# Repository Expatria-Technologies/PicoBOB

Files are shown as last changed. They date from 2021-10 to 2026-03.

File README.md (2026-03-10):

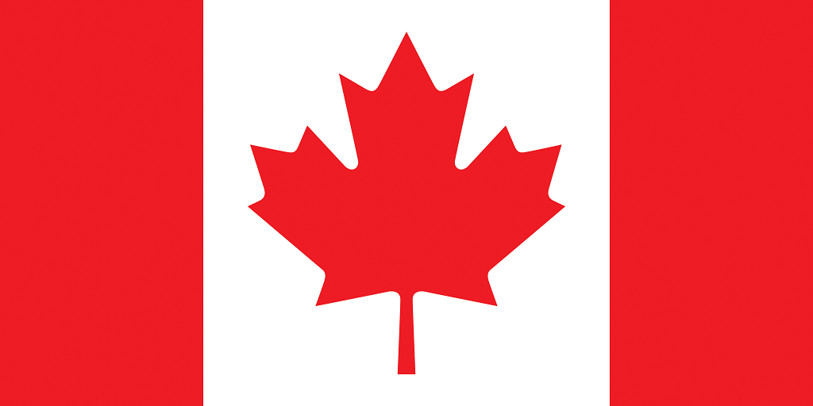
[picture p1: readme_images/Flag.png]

### Canadian-designed open source hardware. For everyone.

# PicoBOB for GRBLHAL

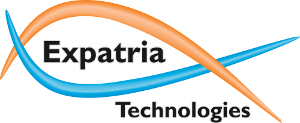
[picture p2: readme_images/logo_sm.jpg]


Expatria Technologies PicoBOB GRBLHAL module

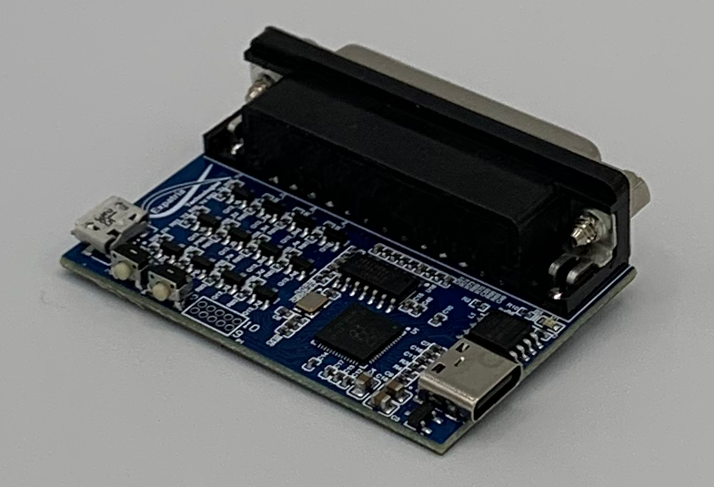
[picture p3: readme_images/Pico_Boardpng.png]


Currently available in our online store:

https://expatria.myshopify.com/products/picobob

Please consider buying a board to support our open-source designs. 

The PicoBOB allows you to use the high performance GRBLHAL motion control system with a traditional Mach3/LinuxCNC parallel-port breakout board.  It is intended to be simple and low cost.  It uses a Raspberry Pi RP2040 MCU and the widely available 5 axis Mach3 breakout board.  It can also be used with the Gecko G540.  The PicoBOB can be easily sourced from JLCPCB.  The complete BOM and fabrications files are in the CAM_OUTPUTS folder for upload.  The design is free to use by all parties, including commercial parties, under the CERN-OHL-S V2 license.  It is our hope that the community finds the design useful and that it may be carried forward to help advance the PrintNC and broader CNC hobby community.

The PicoBOB closely tracks the features of the Mach3 BOB:

1) Up to 5 axes of step/direction control.
3) 10A Spindle relay control.
4) 0-10V analog spindle speed control.
5) 5 general purpose inputs
6) One general purpose output.

The default GRBLHAL builds for the PicoBOB include the following features that are implemented in the RP2040 port of GRBLHAL:

1) Backlash Compensation.
2) Stress-free Autosquaring for the ganged axis
3) Ganged axis offsets to correct for offset homing switches
4) Step rates tested up to 180 KHz on 5 simultaneous axes.

In addition, the board has a USB micro connector for the 5V that is required for the BOB.  There is also a push button to reset the Pi Pico without disconnecting power.

Gerber output files are in the CAM_OUTPUTS folder, along with BOM and Pick and Place files to facilitate easy ordering from JLCPCB.  Now available as a chip-down design in revision B1.  Older A1 revision for Pi Pico module is still hosted in case you want to do the final soldering by hand.  The two designs are functionally identical.

## PicoBOB Overview

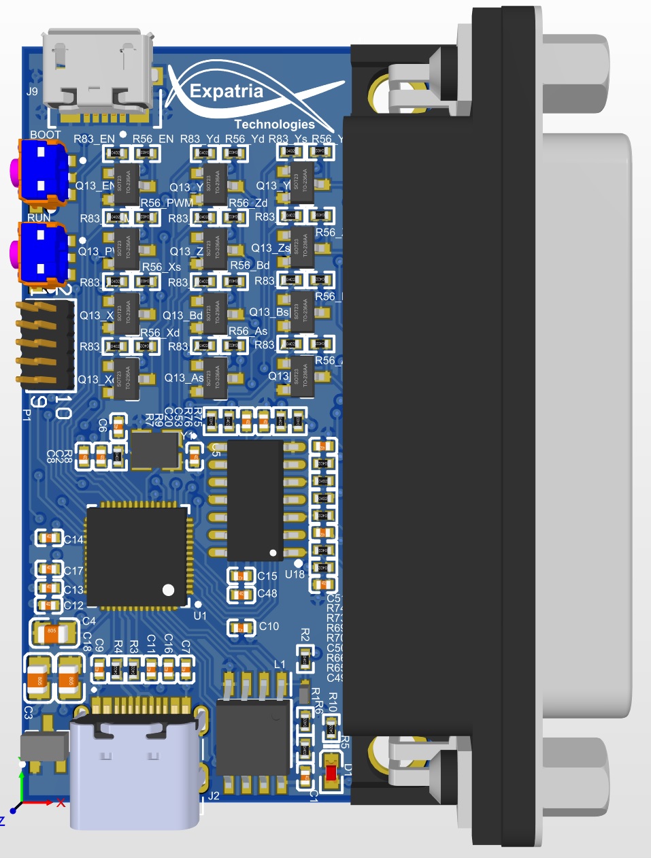
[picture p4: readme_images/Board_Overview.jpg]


Usage notes:

Communication with GRBLHAL on the PicoBOB is accomplished via the USBC connection on the PicoBOB (not connected in above images).  A short USB cable is used to provide the required 5V for the BOB.  In addition, the BOB requires an external 12-24V supply.

The Mach3 BOB shares the B axis direction signal with a spindle relay enable signal - only one can be used at a time.  Also on the PicoBOB, the stepper enable signal is modified in the GRBLHAL default map file so that it is used as the coolant output signal.  All of this is configurable by re-building the GRBLHAL firwmare.

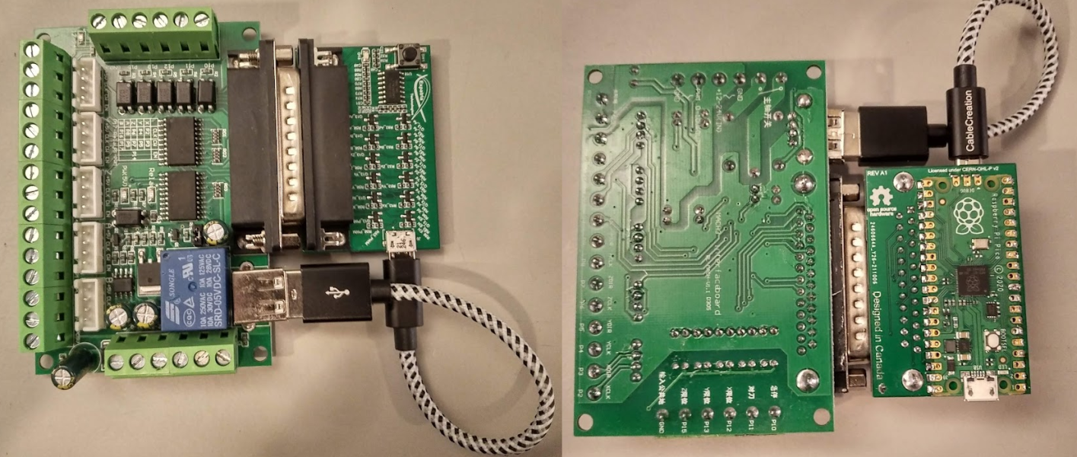
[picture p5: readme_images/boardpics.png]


Above shows the PicoBOB A1 with a Pi Pico installed and connected to the Mach3/LinuxCNC parallel BOB.



Above shows the PicoBOB B1 connected to the Mach3/LinuxCNC parallel BOB.

YGANG pinout is as below:

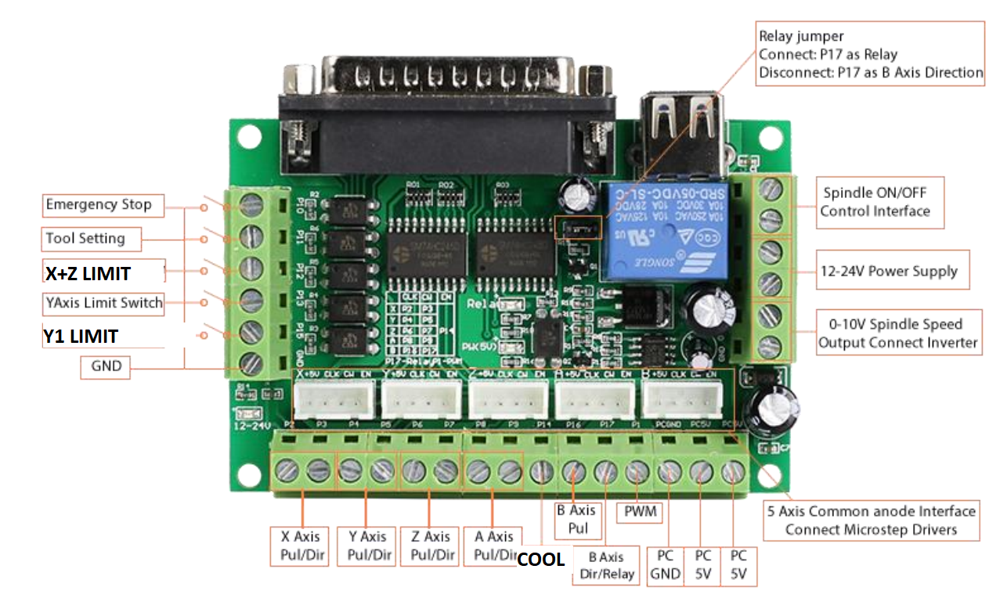
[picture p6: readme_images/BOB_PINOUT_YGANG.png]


To build mainline GRBLHAL firmware, PicoBOB is fully supported by the Web Builder from TerjeIO

http://svn.io-engineering.com:8080/?driver=RP2040&board=PicoBOB

## Gecko Drive G540 support Overview
By using a common "mini gender changer" the PicoBOB can be adapted for use with a G540 4-AXIS Digital Step Drive.

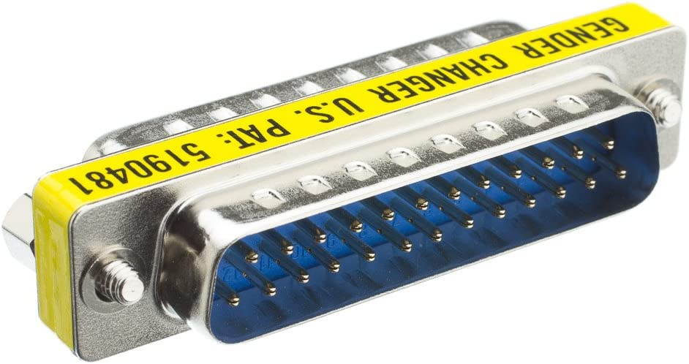
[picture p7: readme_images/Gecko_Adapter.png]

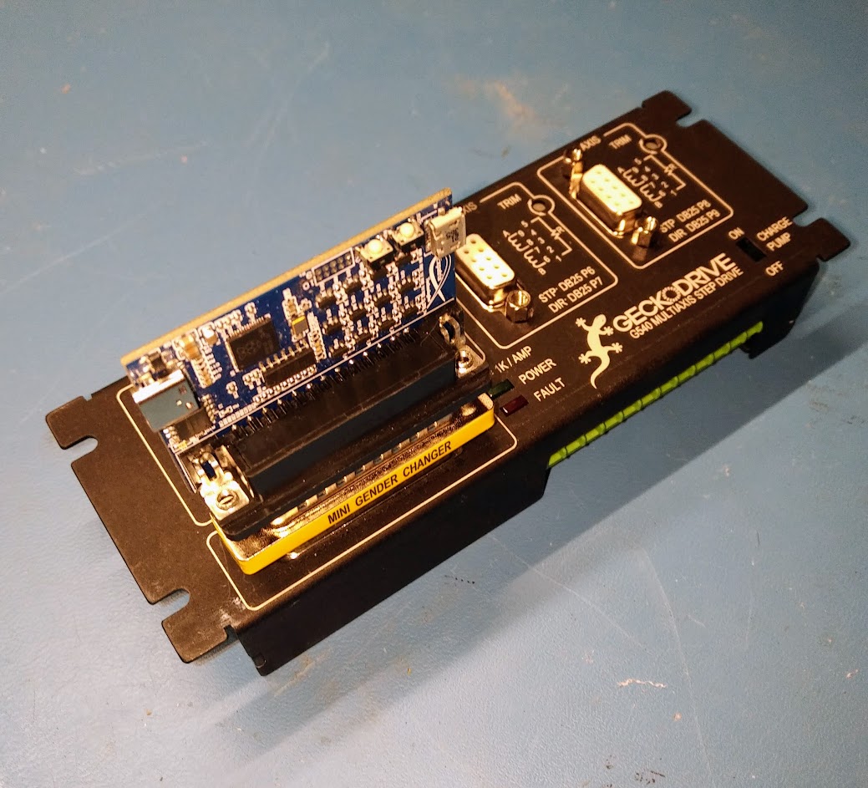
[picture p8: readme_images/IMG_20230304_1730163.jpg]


The updated GRBLHAL map file has the following pinout:

| DB25 Pin | G540 Function | GRBLHAL Function | RP2040 GPIO |
|---|---|---|---|
| Pin 1 | OUTPUT 2 | SPINDLE ENABLE | GPIO14 |
| Pin 2 | X STEP | X STEP | GPIO17 |
| Pin 3 | X DIR | X DIR | GPIO9 |
| Pin 4 | Y SETP | Y SETP | GPIO18 |
| Pin 5 | Y DIR | Y DIR | GPIO10 |
| Pin 6 | Z STEP | Z STEP | GPIO19 |
| Pin 7 | Z DIR | Z DIR | GPIO11 |
| Pin 8 | A STEP | A/M3 STEP | GPIO20 |
| Pin 9 | A DIR | A/M3 DIR | GPIO12 |
| Pin 10 | INPUT 1 | LIMIT XYZ | GPIO3 |
| Pin 11 | INPUT 2 | PROBE | GPIO4 |
| Pin 12 | INPUT 3 | LIMIT A/M3 | GPIO2 |
| Pin 13 | INPUT 4 | HOLD | GPIO1 |
| Pin 14 | VFD PWM | SPINDLE PWM | GPIO16 |
| Pin 15 | FAULT (INPUT 5) | HALT | GPIO5 |
| Pin 16 | CHARGE PUMP | N/A | GPIO21 |
| Pin 17 | OUTPUT 1 | COOLANT | GPIO13 |
| Pin 18-25| GND | | |

For custom builds using the above pinout, you can use this variant from the Web Builder:

http://svn.io-engineering.com:8080/?driver=RP2040&board=PicoBOB_G540

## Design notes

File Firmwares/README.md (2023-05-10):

# Prebuilt PicoBOB Firmwares

Suggestion is to use the aweseom web builder from IO Engineering.

Breakout Board pin mapping:
http://svn.io-engineering.com:8080/?driver=RP2040&board=PicoBOB

Gecko G540 pin mapping:
http://svn.io-engineering.com:8080/?driver=RP2040&board=PicoBOB_G540

Some older testing firmwares are here to help get things up and running.

grblHAL_PicoBOB_3Axis_xxxx.uf2 is for a basic 3 axis machine.

grblHAL_PicoBOB_Ygang__xxxx.uf2 has a ganged Y axis.  This is used on machines like the PrintNC.

grblHAL_PicoBOB_G540YGANG_221229.uf2 has a ganged Y axis and is updated to support the Gecko G540

Install the firmware by putting the Pi Pico into loading mode and copy them to the USB drive that appears.  The PicoBOB is equipped with a reset button for convenience.  With the Pi pico connected to your PC via USB, hold the white button the the Pico and then pulse the black reset button on the other side of the board. The Pico should appear as a USB drive and you can simply copy the desired firmware.

YGANG pinout is as below:



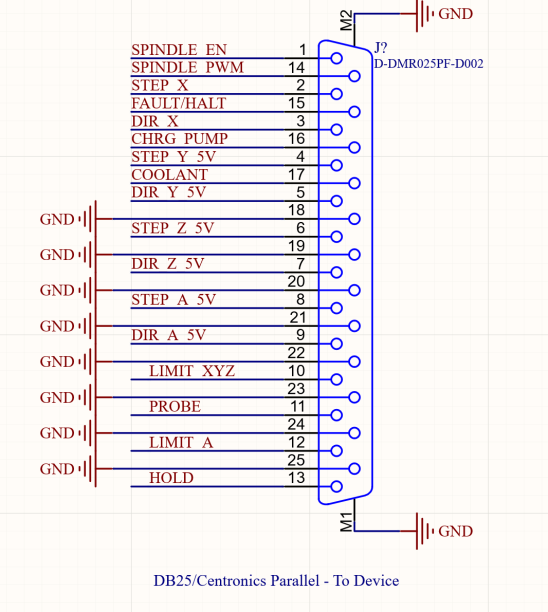
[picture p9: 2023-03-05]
readme_images/g540_pinout.png

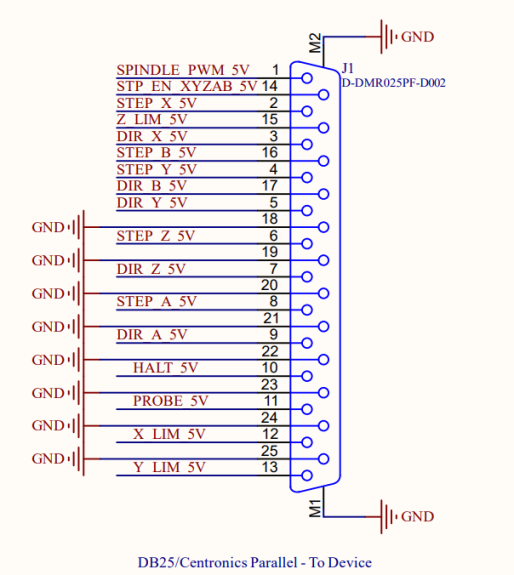
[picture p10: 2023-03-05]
readme_images/picoBOB_Pinout.png

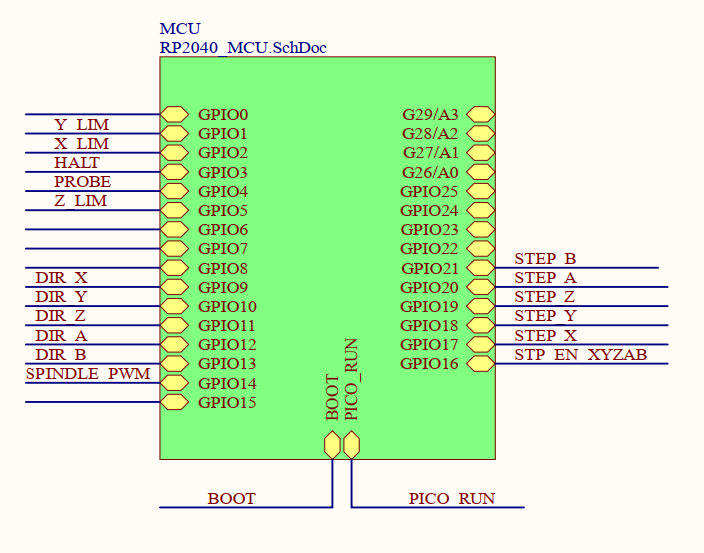
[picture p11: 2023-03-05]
readme_images/default_pinout.png

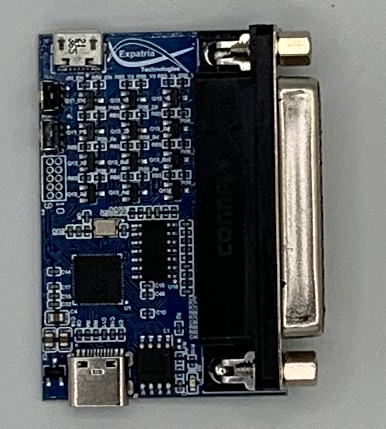
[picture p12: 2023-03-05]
readme_images/Pico_Top.png

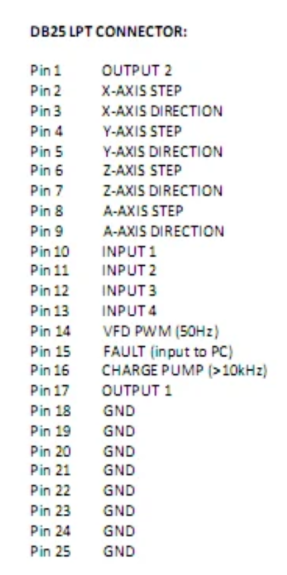
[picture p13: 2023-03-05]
readme_images/G540_DB25_ref.png

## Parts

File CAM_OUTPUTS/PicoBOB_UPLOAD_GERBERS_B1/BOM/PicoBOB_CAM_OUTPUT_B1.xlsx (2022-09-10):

Comment | Description | Designator | Footprint | SuppliersPartNumber | Quantity
100nF | Chip capacitors | C1, C7, C8, C11, C12, C13, C14, C15, C16, C17 | 0402_C | C1525 | 10
4.7uF | Chip capacitor | C2 | 0402_C | C23733 | 1
22uF | Chip capacitors | C3, C4, C18 | 0805_C | C129303 | 3
10pF | Chip capacitors | C5, C6 | 0402_C | C32949 | 2
1.0uF | Chip capacitor | C9, C10, C48 | 0402_C | C52923 | 3
10nF | Chip capacitors | C20, C49, C50, C51, C53 | 0402_C | C15195 | 5
0603 Green | LED | D1 | 0603_LED_S1 | C72043 | 1
D-DMR025PF-D002 | Through Hole,P=2.77mm D-Sub Connectors ROHS | J1 | 618025231121 | C77838 | 1
TYPE-C-31-M-12 | USB Connectors 24 Receptacle 1 8.94*7.3mm RoHS | J2 | HRO_TYPE-C-31-M-12 | C165948 | 1
473460001 | CONN RCPT USB2.0 MICRO B SMD R/A | J9 | FP-473460001-MFG | C132560 | 1
W25Q128JVSIQ_TR | Inductor | L1 | SOIC127P780X195-8N | C97521 | 1
MMBT5551 G1 | 三极管 | Q13_Ad, Q13_As, Q13_Bd, Q13_Bs, Q13_EN, Q13_PWM, Q13_Xd, Q13_Xs, Q13_Yd, Q13_Ys, Q13_Zd, Q13_Zs | SOT-23(SOT-23-3) | C2145 | 12
DNP | Resistor, ±5%, 0.05W | R1 | 0402 |  | 1
1KΩ ±1% | Chip resistor | R2 | 0402_R | C11702 | 1
22Ω ±1% | Chip resistor | R3, R4 | 0402_R | C25092 | 2
5.1KΩ ±1% | Chip resistor | R5, R6, R10 | 0402_R | C25905 | 3
100KΩ ±1% | Chip resistor | R7, R65, R69, R73, R75 | 0402_R | C25741 | 5
470Ω ±1% | Chip resistor | R8 | 0402_R | C25117 | 1
510Ω ±1% | Chip resistor | R9, R56_Ad, R56_As, R56_Bd, R56_Bs, R56_EN, R56_PWM, R56_Xd, R56_Xs, R56_Yd, R56_Ys, R56_Zd, R56_Zs, R66, R70, R74, R76 | 0402_R | C25123 | 17
2.2KΩ ±1% | Chip resistor | R83_Ad, R83_As, R83_Bd, R83_Bs, R83_EN, R83_PWM, R83_Xd, R83_Xs, R83_Yd, R83_Ys, R83_Zd, R83_Zs | 0402_R | C25879 | 12
SKRTLAE010 | Side Push Type, 250 V, -40 to 90 degC, 3-Pin SMD, RoHS, Tape and Reel | SW1, SW2 | ALPS-SKRTLAE010_V | C110293 | 2
RP2040 | RP2040 First MCU from RPI | U1 | RP2040 |  | 1
74HC14D | 74系列逻辑芯片 | U18 | SOIC-14_150mil | C5605 | 1
XC6206P332MR | 200mA 680mV@(100mA) Fixed 3.3V~3.3V Positive 1 6V SOT-23-3L Linear Voltage Regulators (LDO) ROHS | VR1 | SOT-23-3L | C5446 | 1
YSX321SL | Crystal or Oscillator | Y1 | YSX321SL | C9002 | 1

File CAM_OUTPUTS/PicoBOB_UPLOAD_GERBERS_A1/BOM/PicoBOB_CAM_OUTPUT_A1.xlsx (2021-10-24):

Comment | Description | Designator | Footprint | SuppliersPartNumber | Quantity
10nF | Chip capacitors | C20, C49, C50, C51, C53 | 0402_C | C15195 | 5
100nF | Chip capacitors | C23 | 0402_C | C1525 | 1
1.0uF | Chip capacitor | C48 | 0402_C | C52923 | 1
0805 Green | LED | D15 | 0805_LED_S1 | C2297 | 1
D-DMR025PF-D002 | Through Hole,P=2.77mm D-Sub Connectors ROHS | J1 | 618025231121 | C190083 | 1
PICO | Connector | J8 | PICO |  | 1
473460001 | CONN RCPT USB2.0 MICRO B SMD R/A | J9 | FP-473460001-MFG | C132560 | 1
MMBT5551 G1 | 三极管 | Q13_Ad, Q13_As, Q13_Bd, Q13_Bs, Q13_EN, Q13_PWM, Q13_Xd, Q13_Xs, Q13_Yd, Q13_Ys, Q13_Zd, Q13_Zs | SOT-23(SOT-23-3) | C2145 | 12
100KΩ ±1% | Chip resistor | R7, R65, R69, R73, R75 | 0402_R | C25741 | 5
510Ω ±1% | Chip resistor | R9, R56_Ad, R56_As, R56_Bd, R56_Bs, R56_EN, R56_PWM, R56_Xd, R56_Xs, R56_Yd, R56_Ys, R56_Zd, R56_Zs, R66, R70, R74, R76 | 0402_R | C25123 | 17
10KΩ ±1% | Chip resistor | R52 | 0402_R | C25744 | 1
1.2KΩ ±1% | Chip resistor | R59 | 0402_R | C25862 | 1
2.2KΩ ±1% | Chip resistor | R83_Ad, R83_As, R83_Bd, R83_Bs, R83_EN, R83_PWM, R83_Xd, R83_Xs, R83_Yd, R83_Ys, R83_Zd, R83_Zs | 0402_R | C25879 | 12
K2-1102SP-C4SC-04 | Top Actuated 50mA @ 12VDC Round Button SPST 6*6mm Tactile Switches ROHS | SW1 | TECO-FSM4JSMATR_V | C127509 | 1
74HC14D | 74系列逻辑芯片 | U18 | SOIC-14_150mil | C5605 | 1

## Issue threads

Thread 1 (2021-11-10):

Question: JLCPCB

oke24, 2021-11-10:
Hi , a short question - for SMT Assembly at JLCPCB I need a CPL file.
I couldn't find this file in the PicoBOB directory structure. It it possible to generate this file and copy into the CAM_OUTPUTS folder ? Thanky you very much !

andrewmarles, 2021-11-11:
You should use the csv in the pick and place folder.

oke24, 2021-11-11:
Thanks!

Closed 2021-11-11.

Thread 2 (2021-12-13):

Can this be bought?

Cncninja, 2021-12-13:
anywhere to buy this ?

andrewmarles, 2021-12-13:
Best way to get one is to use the provided files and just order a couple assembled from JLCPCB.

Closed 2021-12-20.

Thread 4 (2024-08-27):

Maximum step rate

jamesbaber, 2024-08-27:
Hello,

I've purchased a PicoBOB and was hoping to utilise the claimed maximum step rate of 180k steps/sec.
My oscilloscope shows a stable pulse up until around 60 kHz with very narrow gaps between pulses. If I try to continue up to 70 kHz, the pulse gaps disappear and it becomes one solid pulse with a few glitches.

At 60kHz, the gaps are ~490 ns long and exhibit very square edges once passed through the SN74HC245 bus transceivers on the Mach3 BOB. Before the buffer, they have rounder edges and still do not properly form at higher frequencies.
I am trying to jog the board from ioSender 2.0.44.

I've tried the PicoBOB and PicoBOB_G540 boards on the grblHAL Web Builder with the same results.
Can you please let me know what the test conditions were for the 180kHz pulse rate spec?

Thanks!

andrewmarles, 2024-08-27:
You can try reducing the pulse width in your stepper settings.

jamesbaber, 2024-08-27:
@andrewmarles

Thank you, I did not expect such granular controls to exist!
This has resolved my issue.

Closed 2024-08-27.

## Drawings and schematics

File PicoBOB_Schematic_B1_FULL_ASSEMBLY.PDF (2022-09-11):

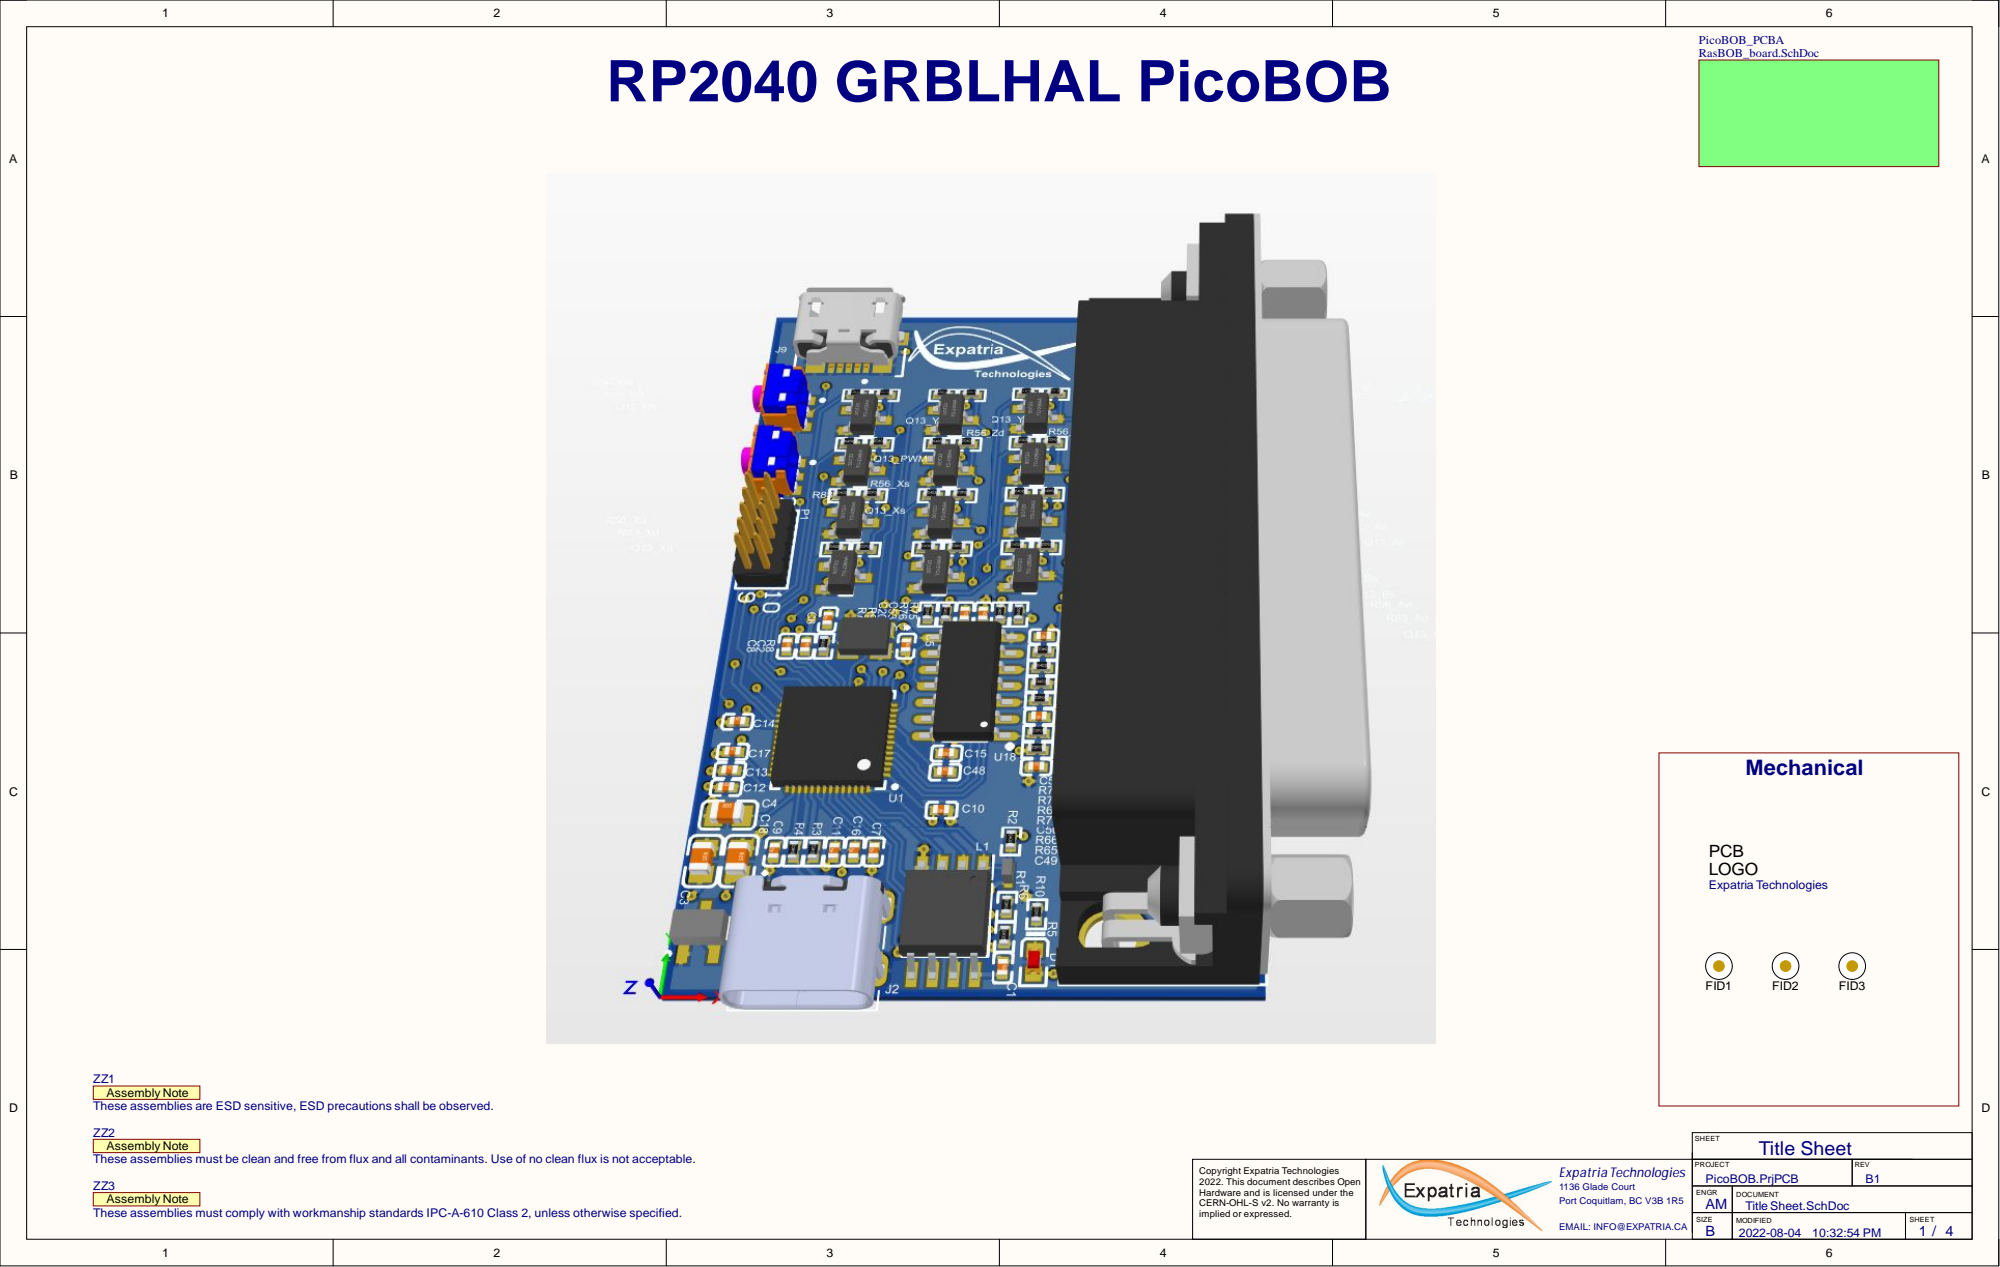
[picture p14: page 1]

Assembly Note
These assemblies are ESD sensitive, ESD precautions shall be observed.

These assemblies must be clean and free from flux and all contaminants. Use of no clean flux is not acceptable.

Copyright Expatria Technologies 2022. This document describes Open Hardware and is licensed under the CERN-OHL-S v2. No warranty is implied or expressed. | | PROJECT PicoBOB.PrjPCB | REV B1

These assemblies must comply with workmanship standards IPC-A-610 Class 2, unless otherwise specified.

ENGR AM | DOCUMENT Title Sheet.SchDoc

SIZE B | MODIFIED 2022-08-04 10:32:54 PM | SHEET 1 / 4

EMAIL: INFO@EXPATRIA.CA

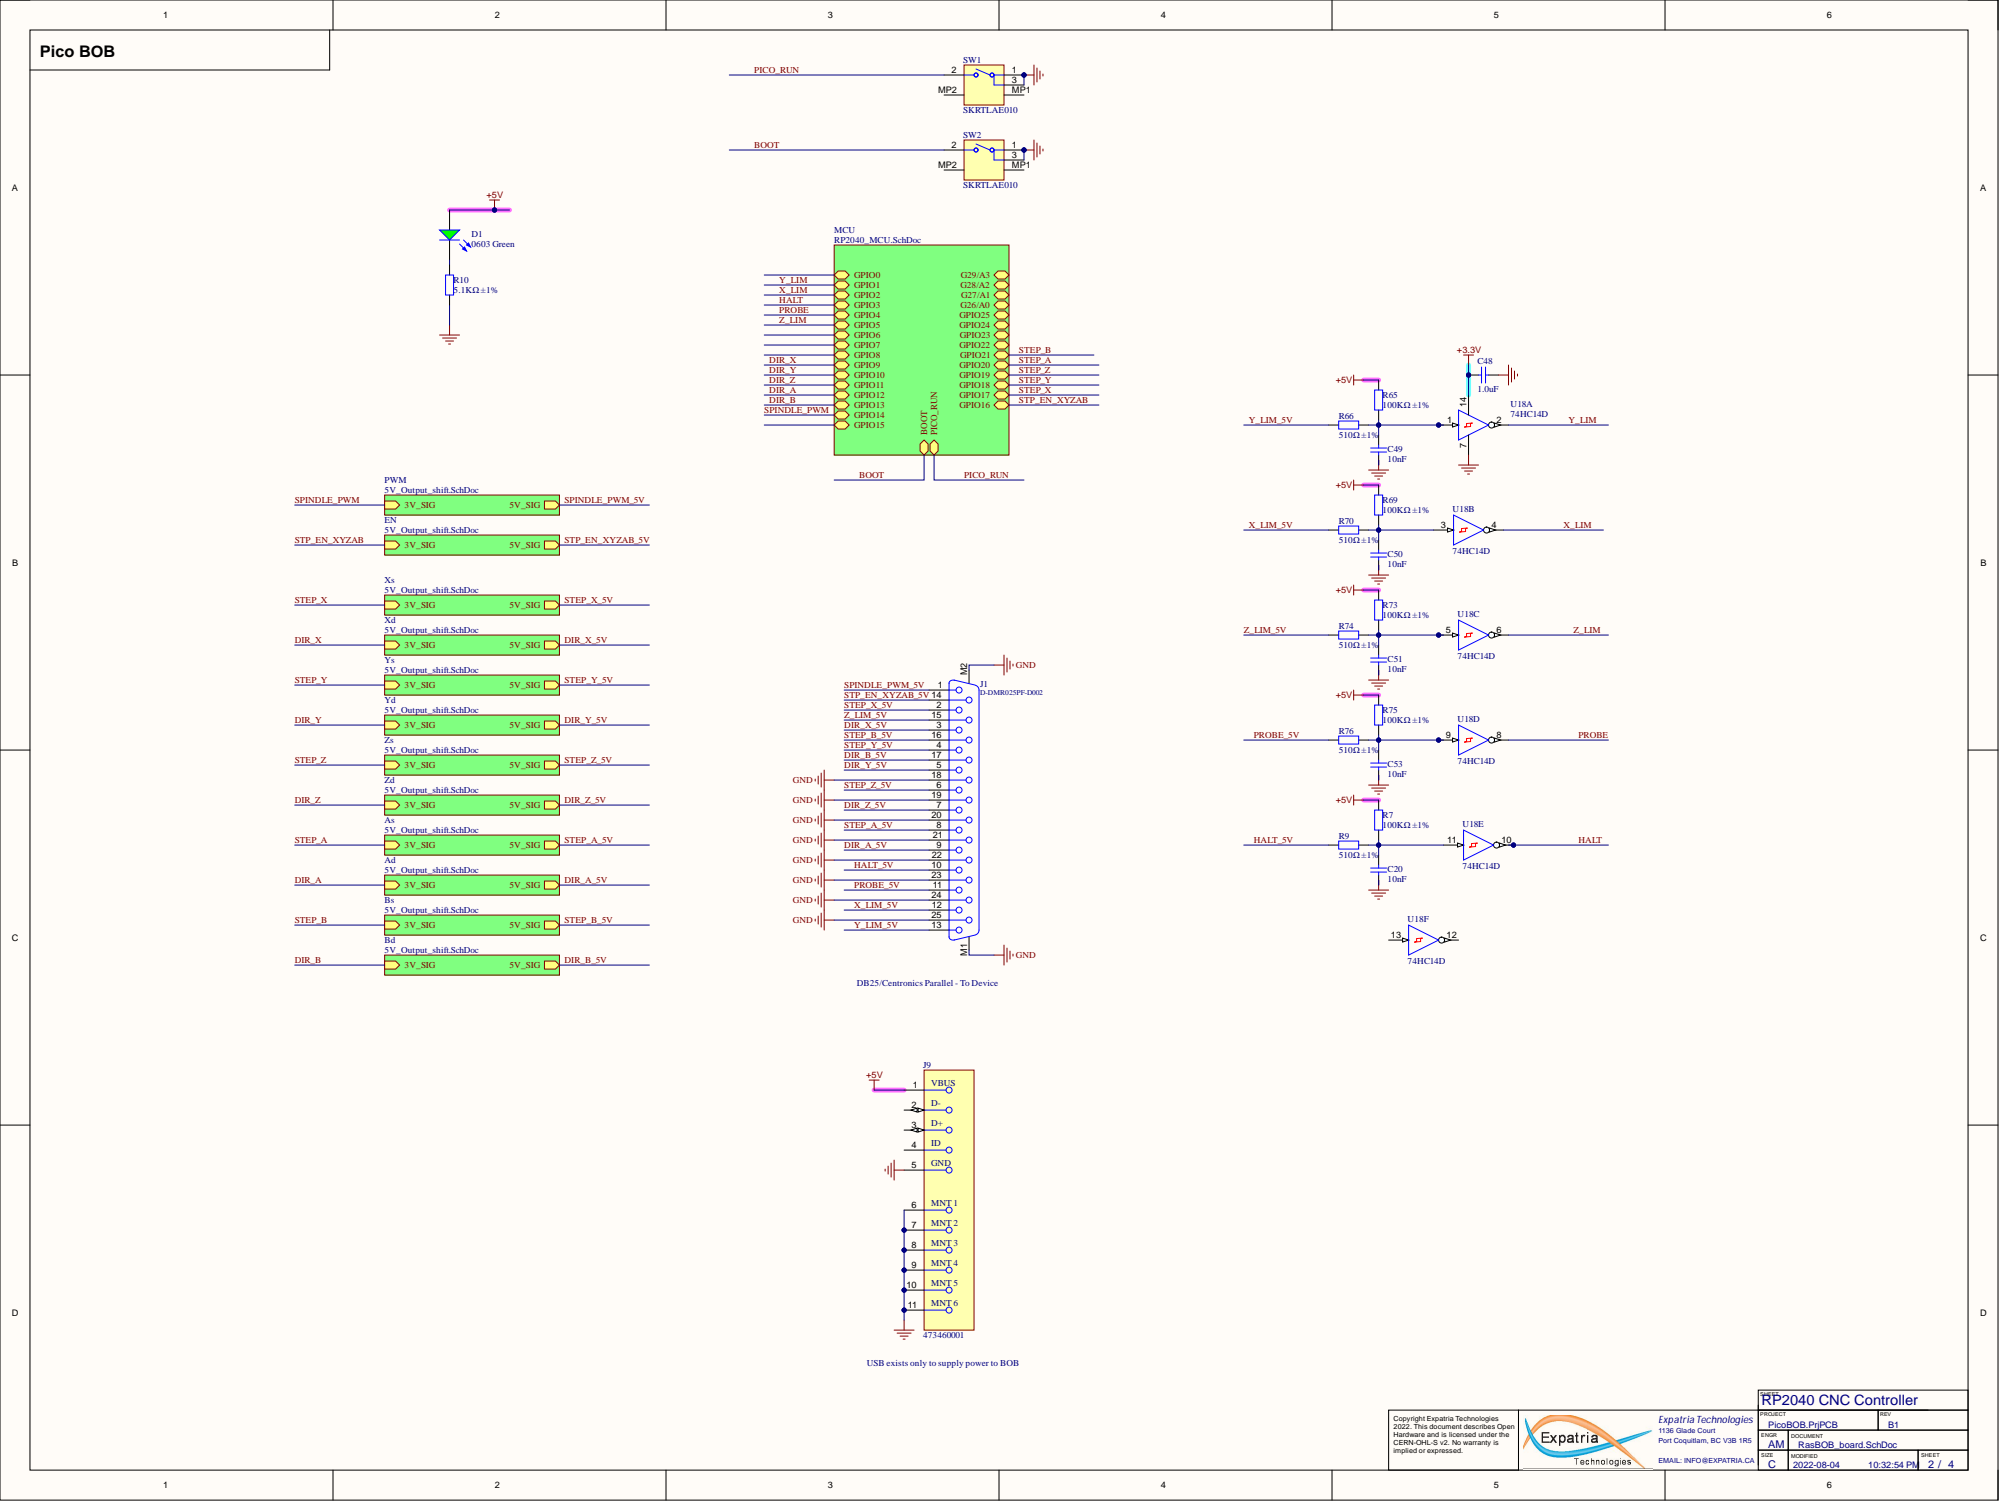
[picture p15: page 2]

Hardware a n d i s l i e s d u er th CERN-OHL-S v 2. No warra nty i m p or x pre . | | P OJE PicoBOB.Prj | R V

B Copyright Expatria Technologies 2022. This document describes Open

N G A | U RasBOB_board.Sc h D o c

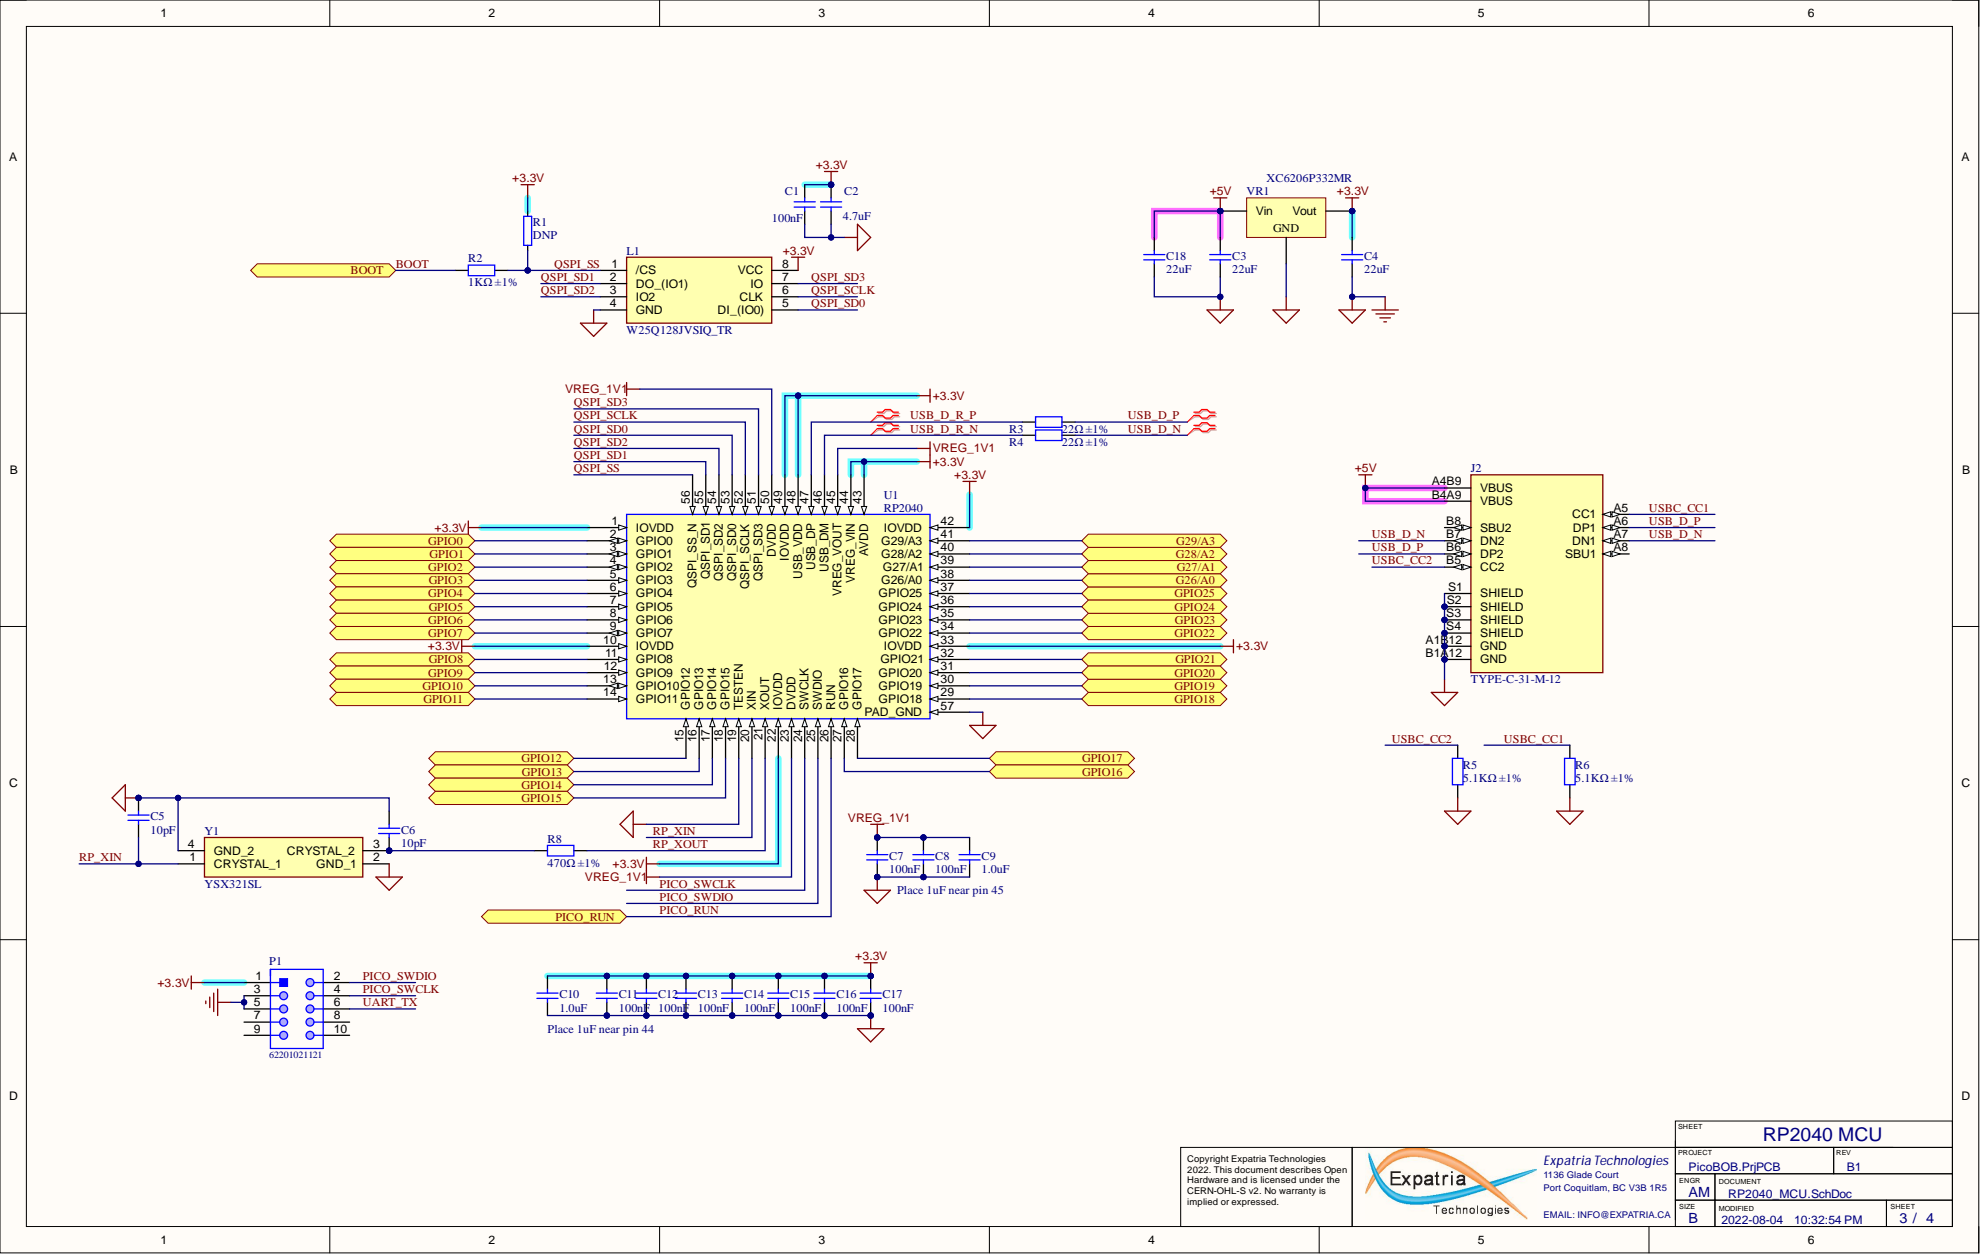
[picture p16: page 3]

QSPI_SD2
QSPI_SD1
QSPI_SS

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

ENGR AM | DOCUMENT RP2040_MCU.SchDoc

SIZE | MODIFIED 2022-08-04 10:32:54 PM | SHEET 3 / 4

EMAIL: INFO@EXPATRIA.CA

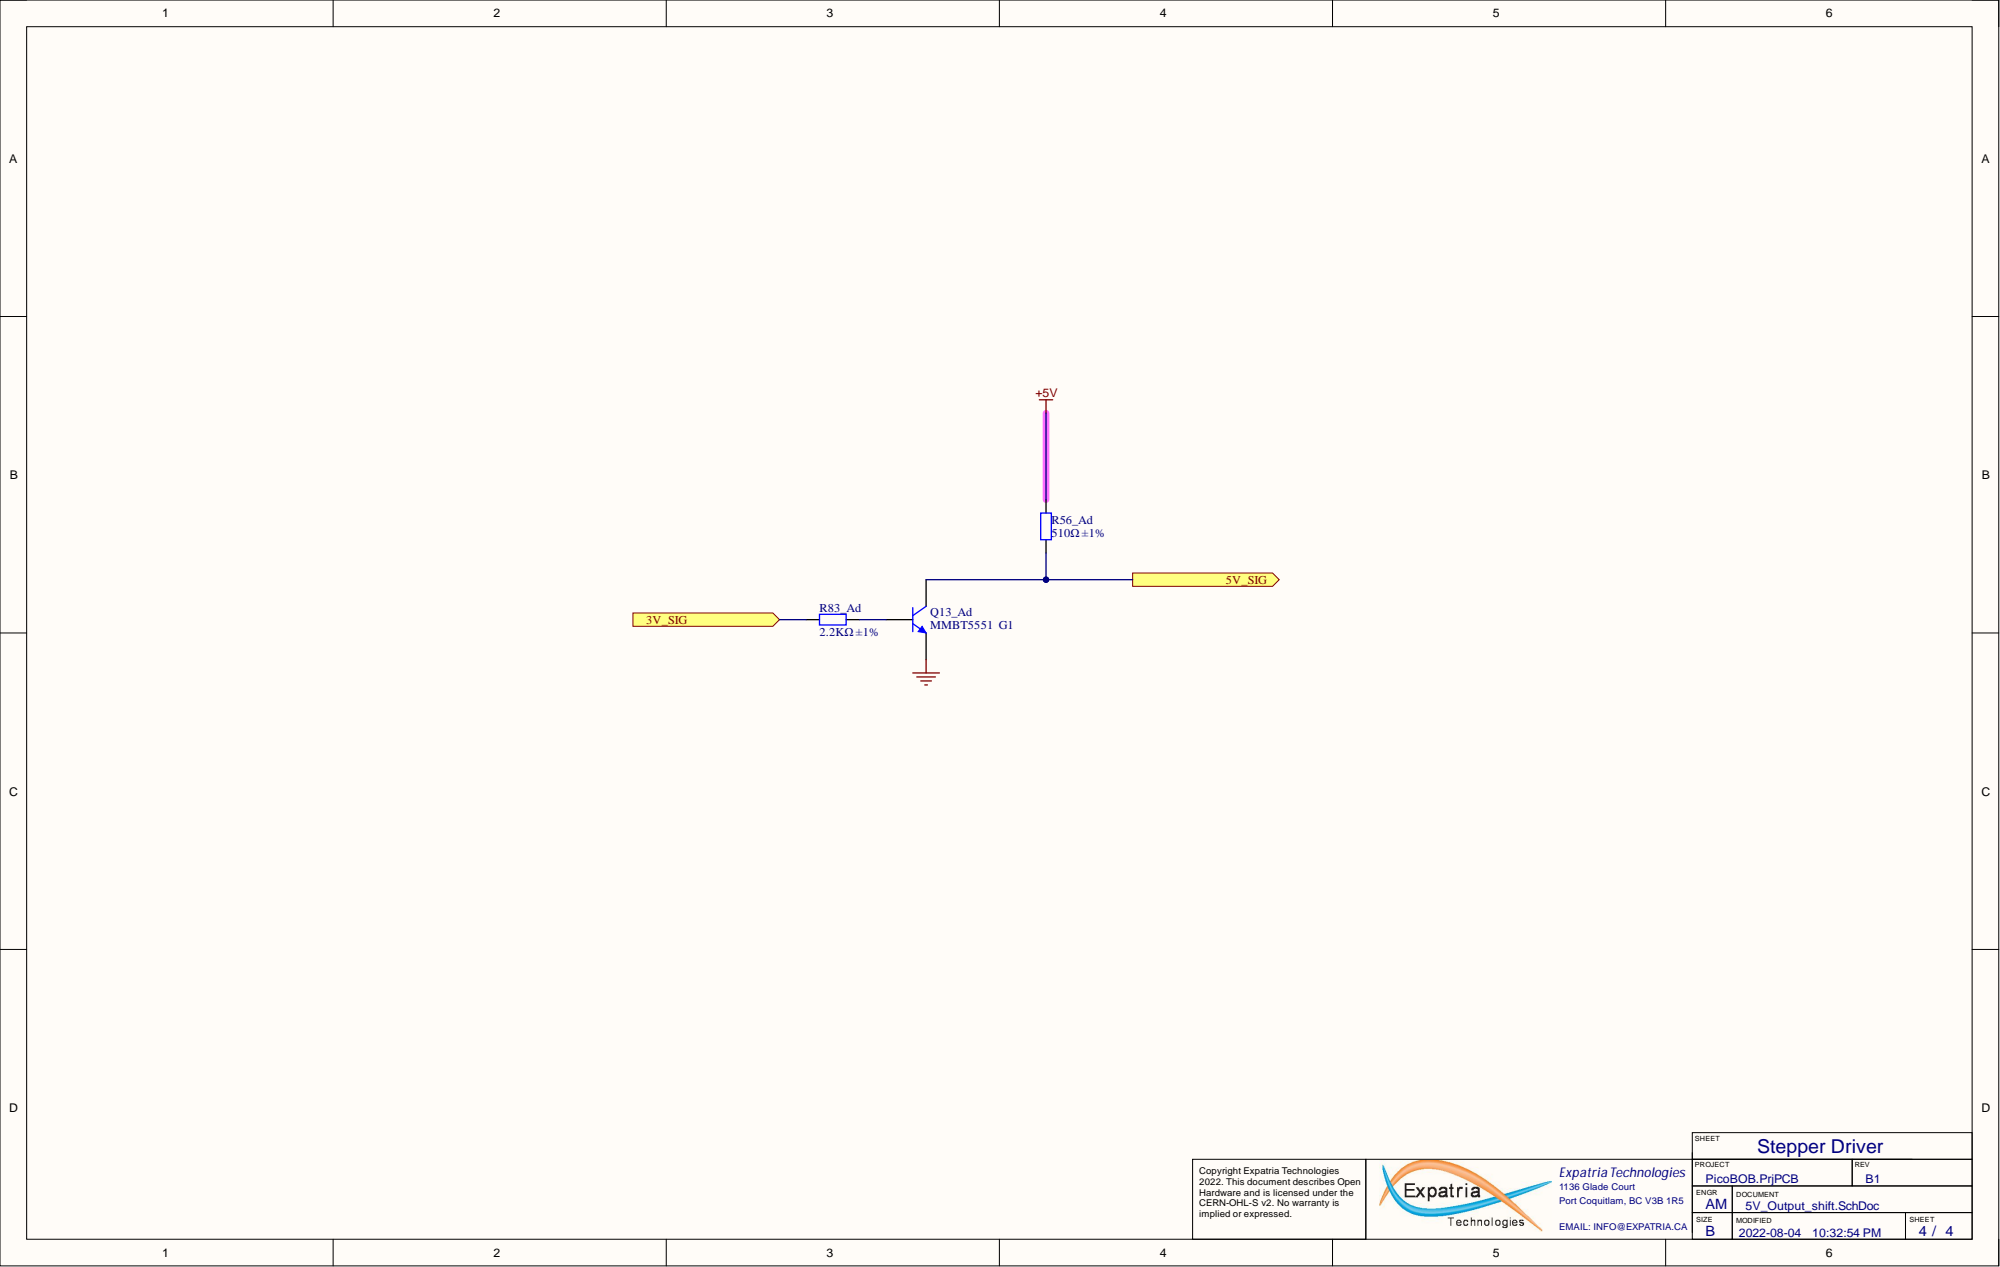
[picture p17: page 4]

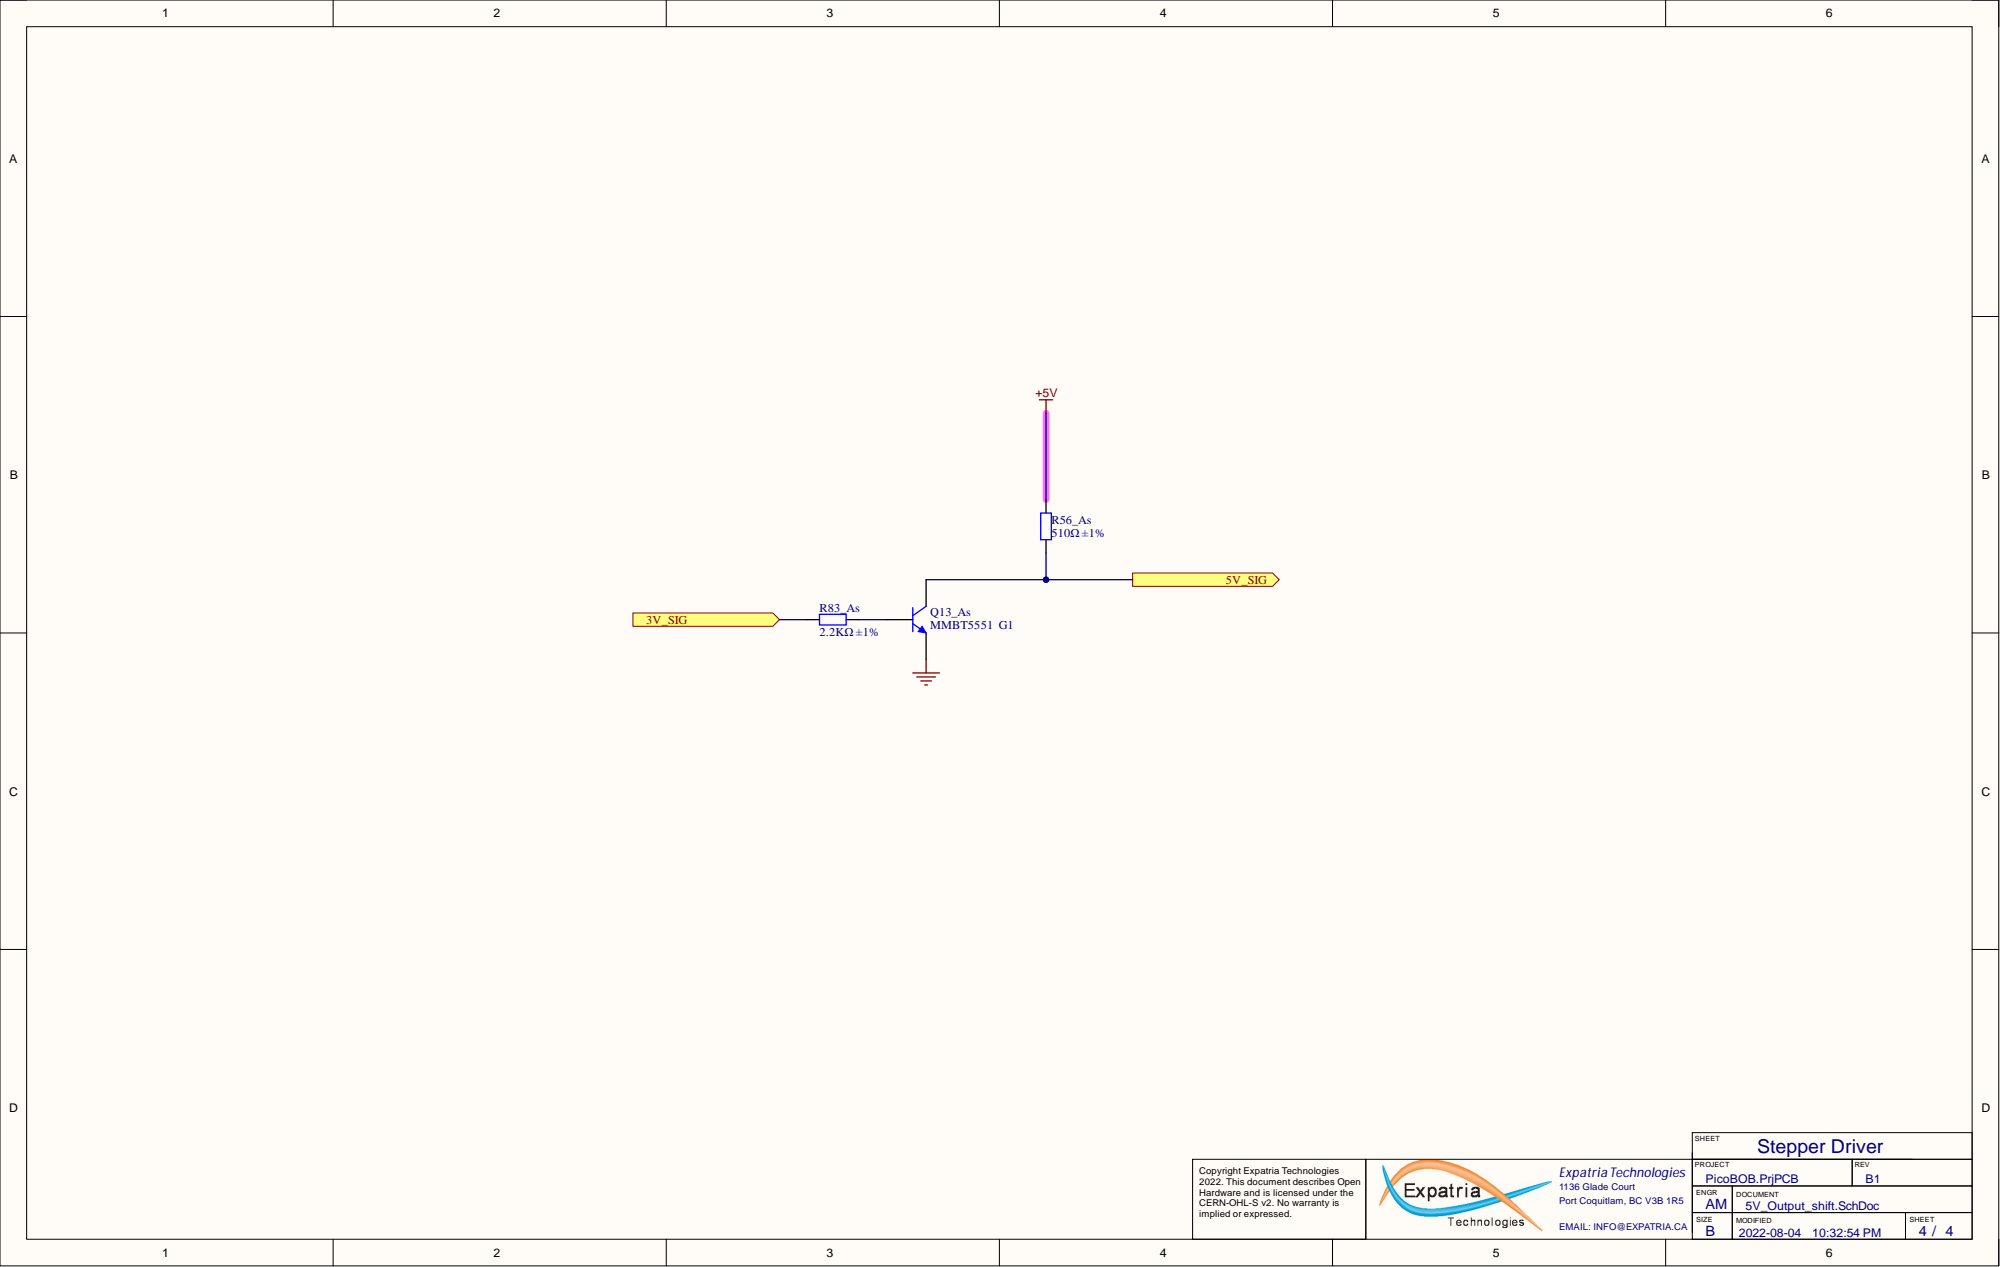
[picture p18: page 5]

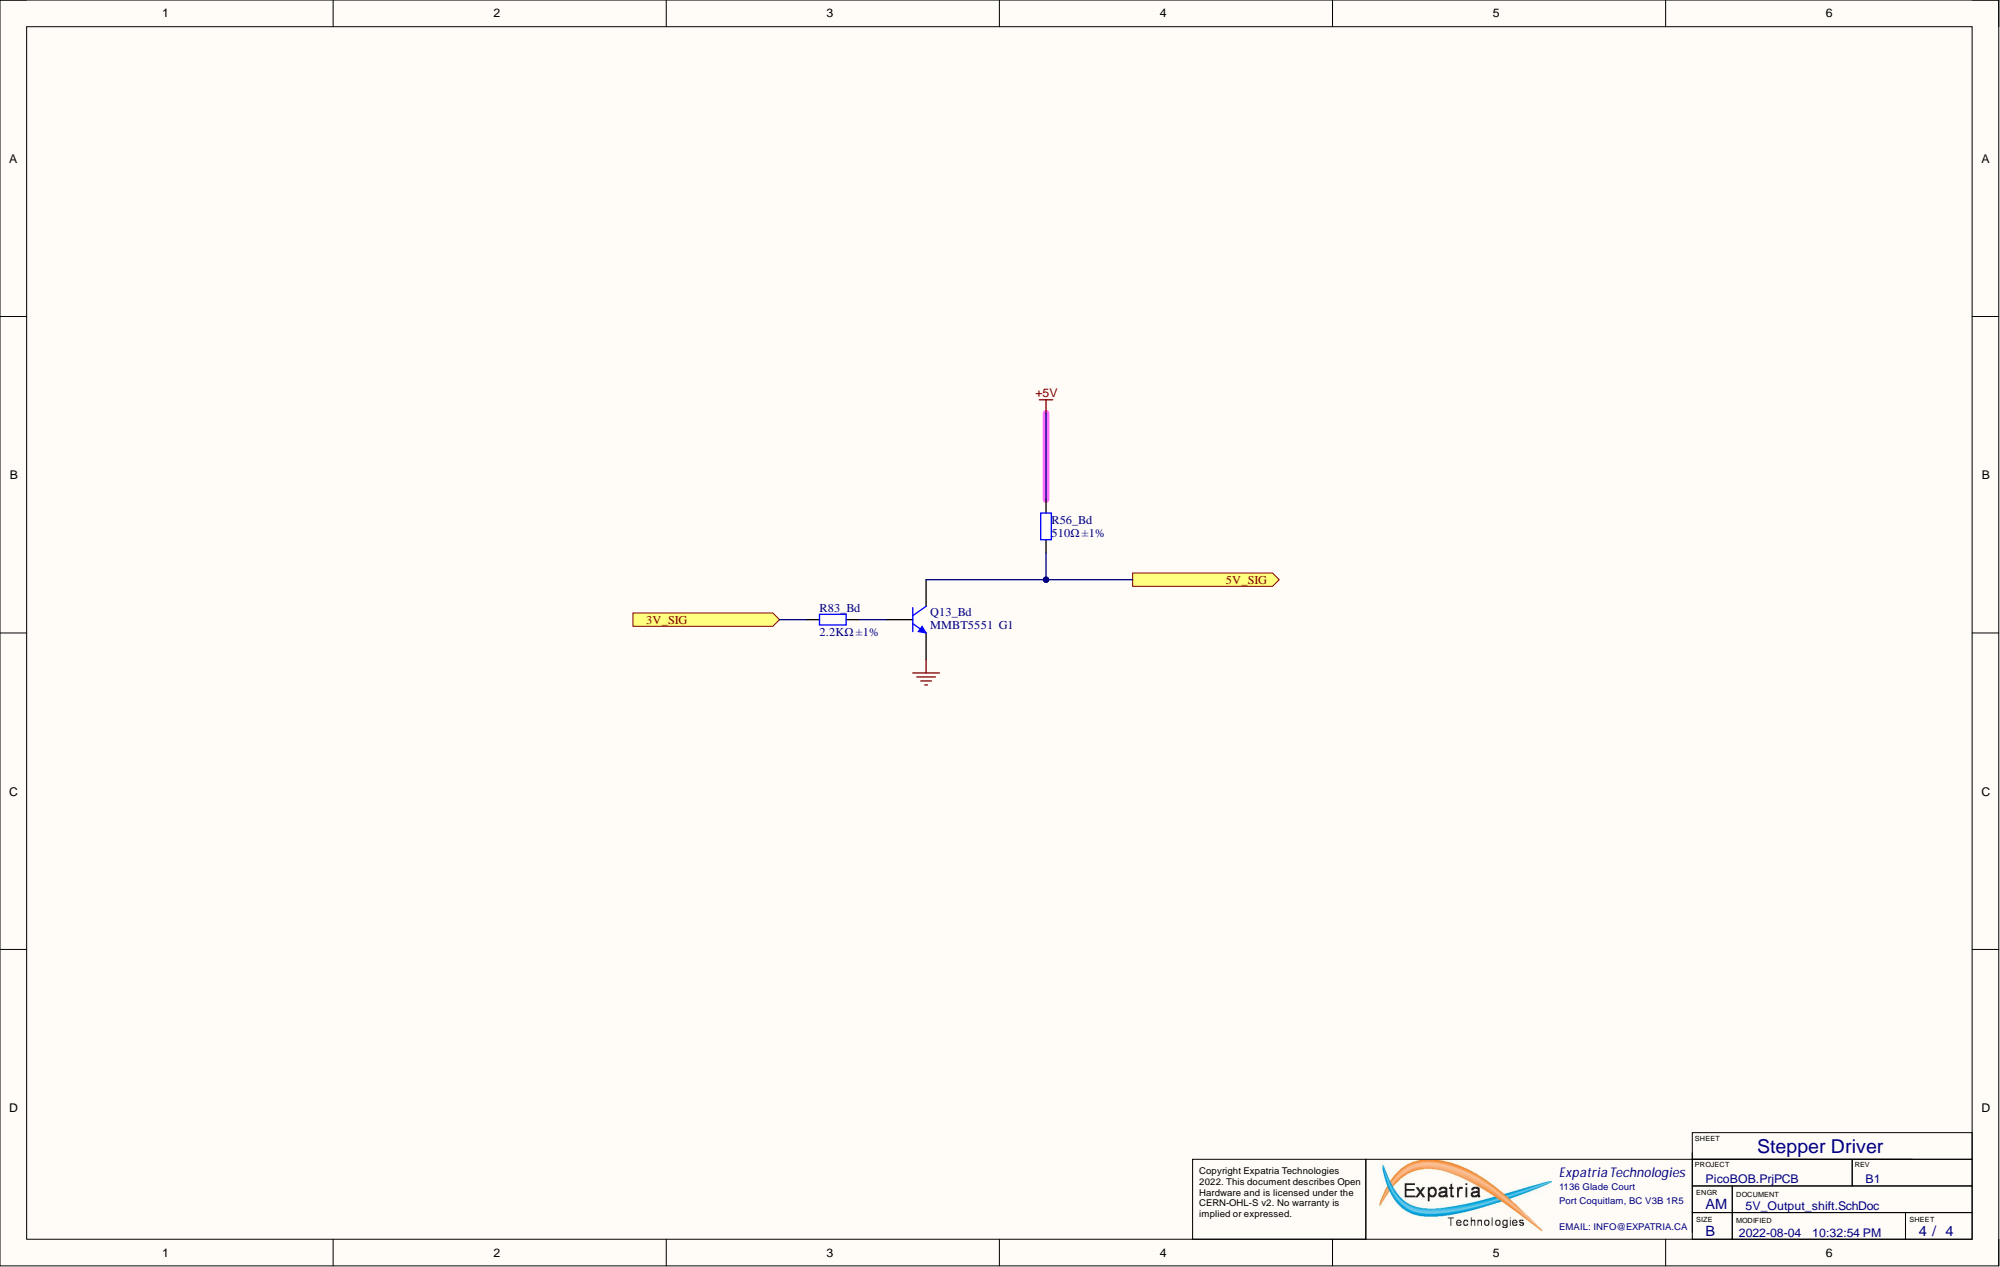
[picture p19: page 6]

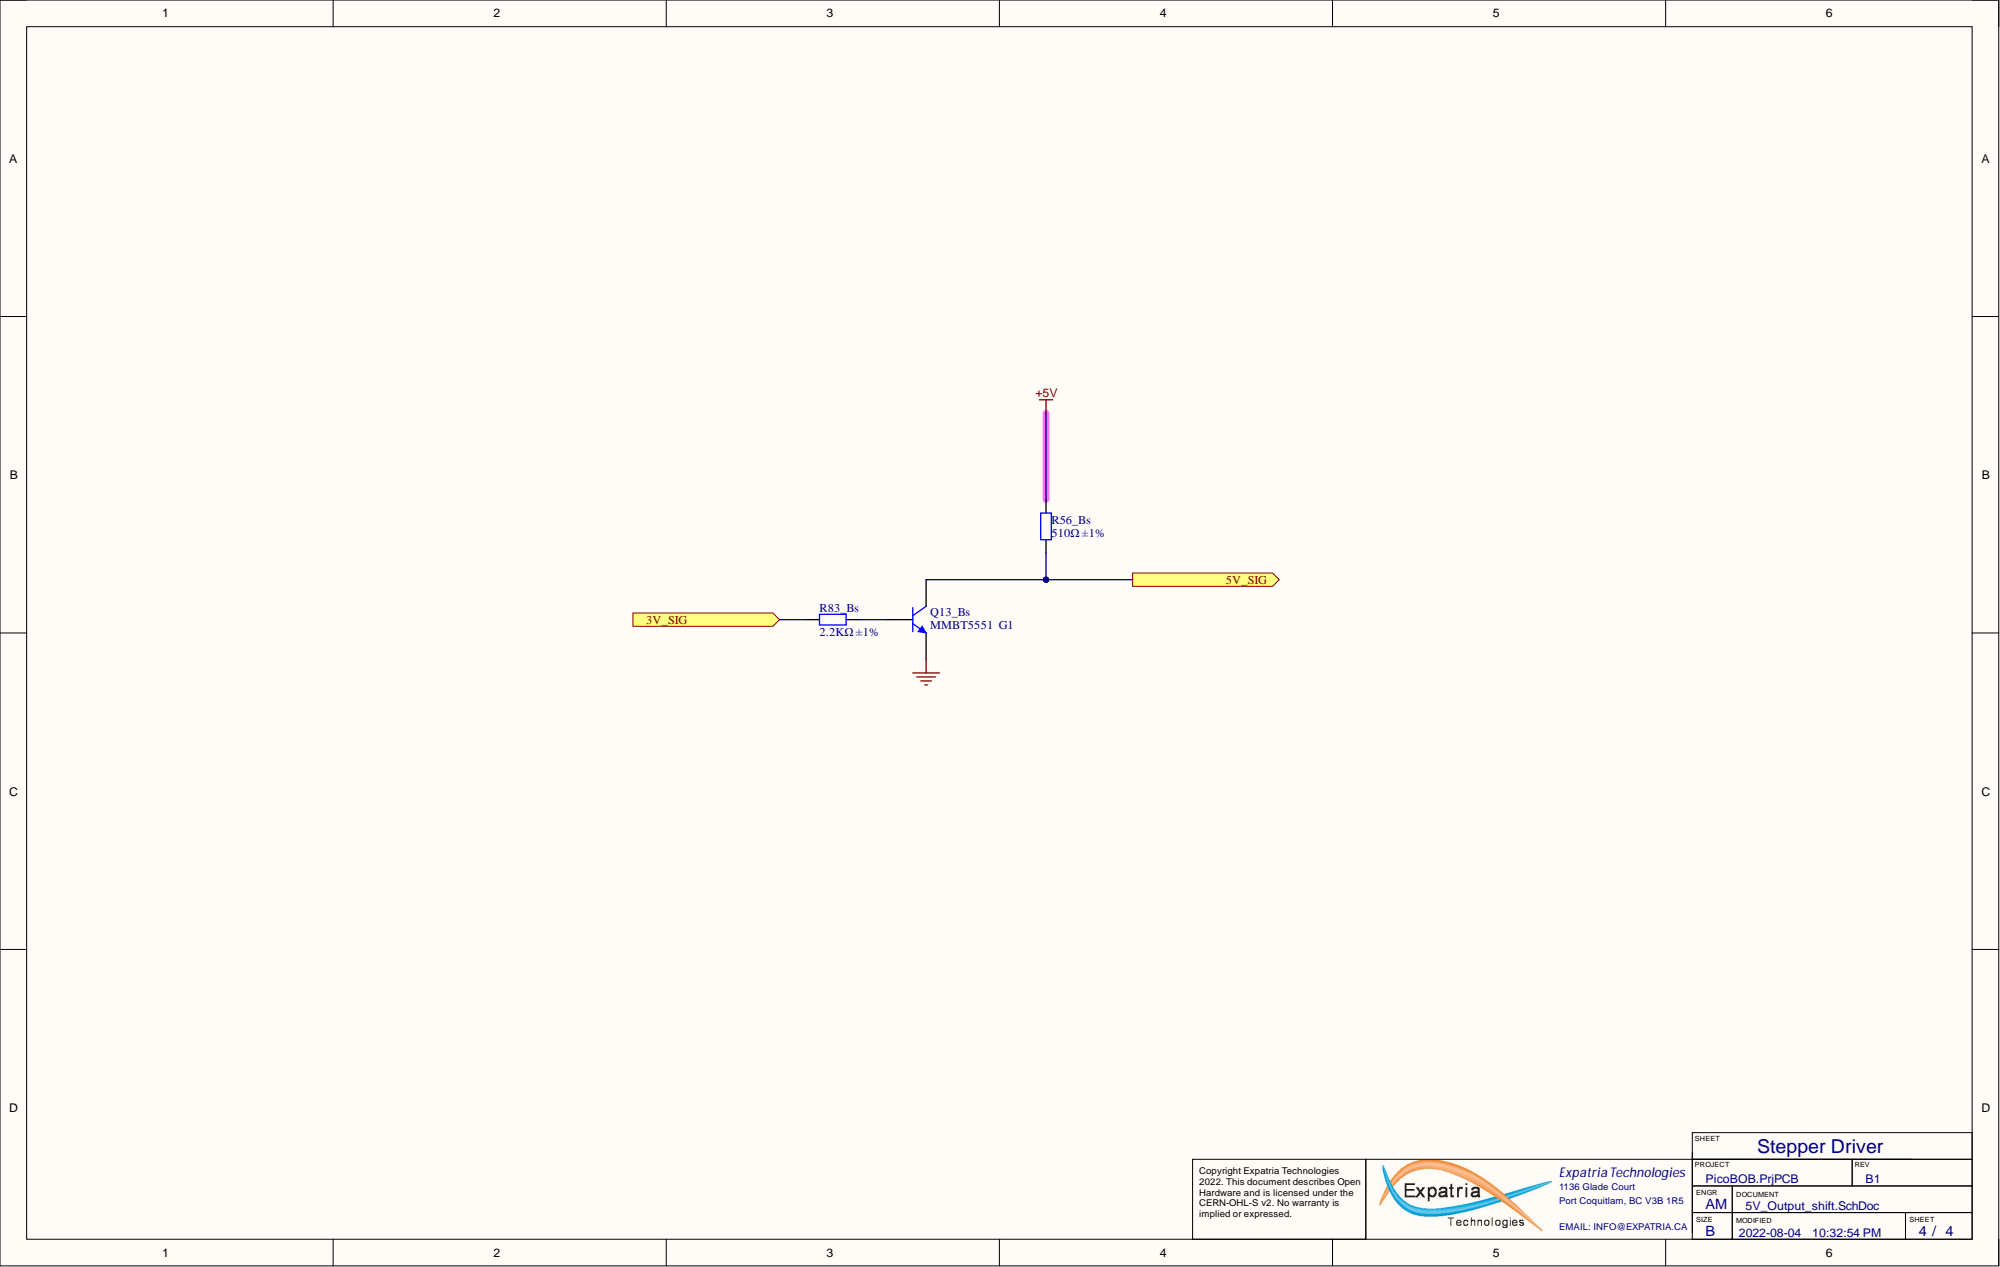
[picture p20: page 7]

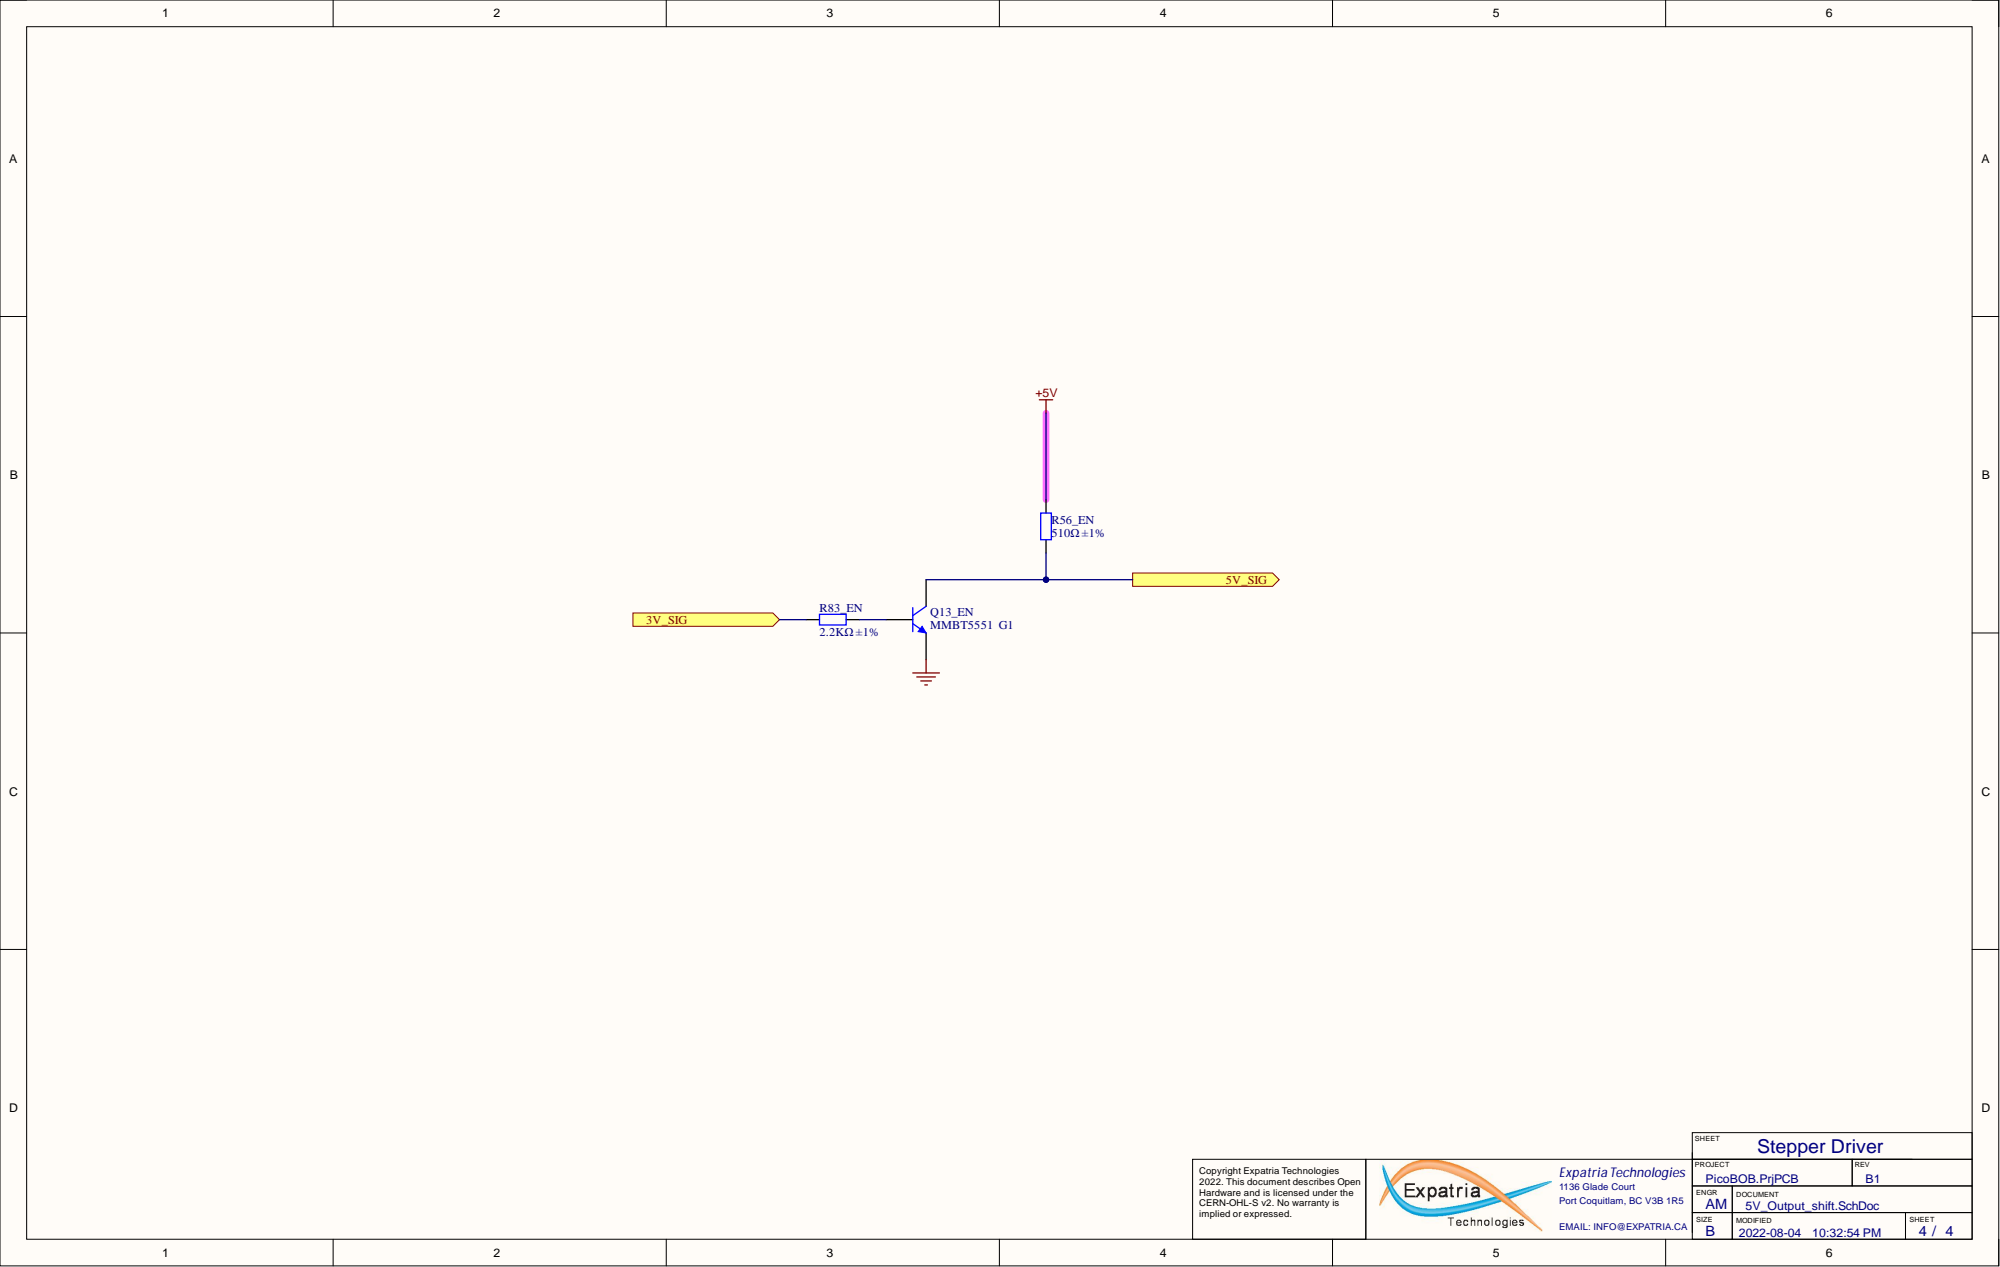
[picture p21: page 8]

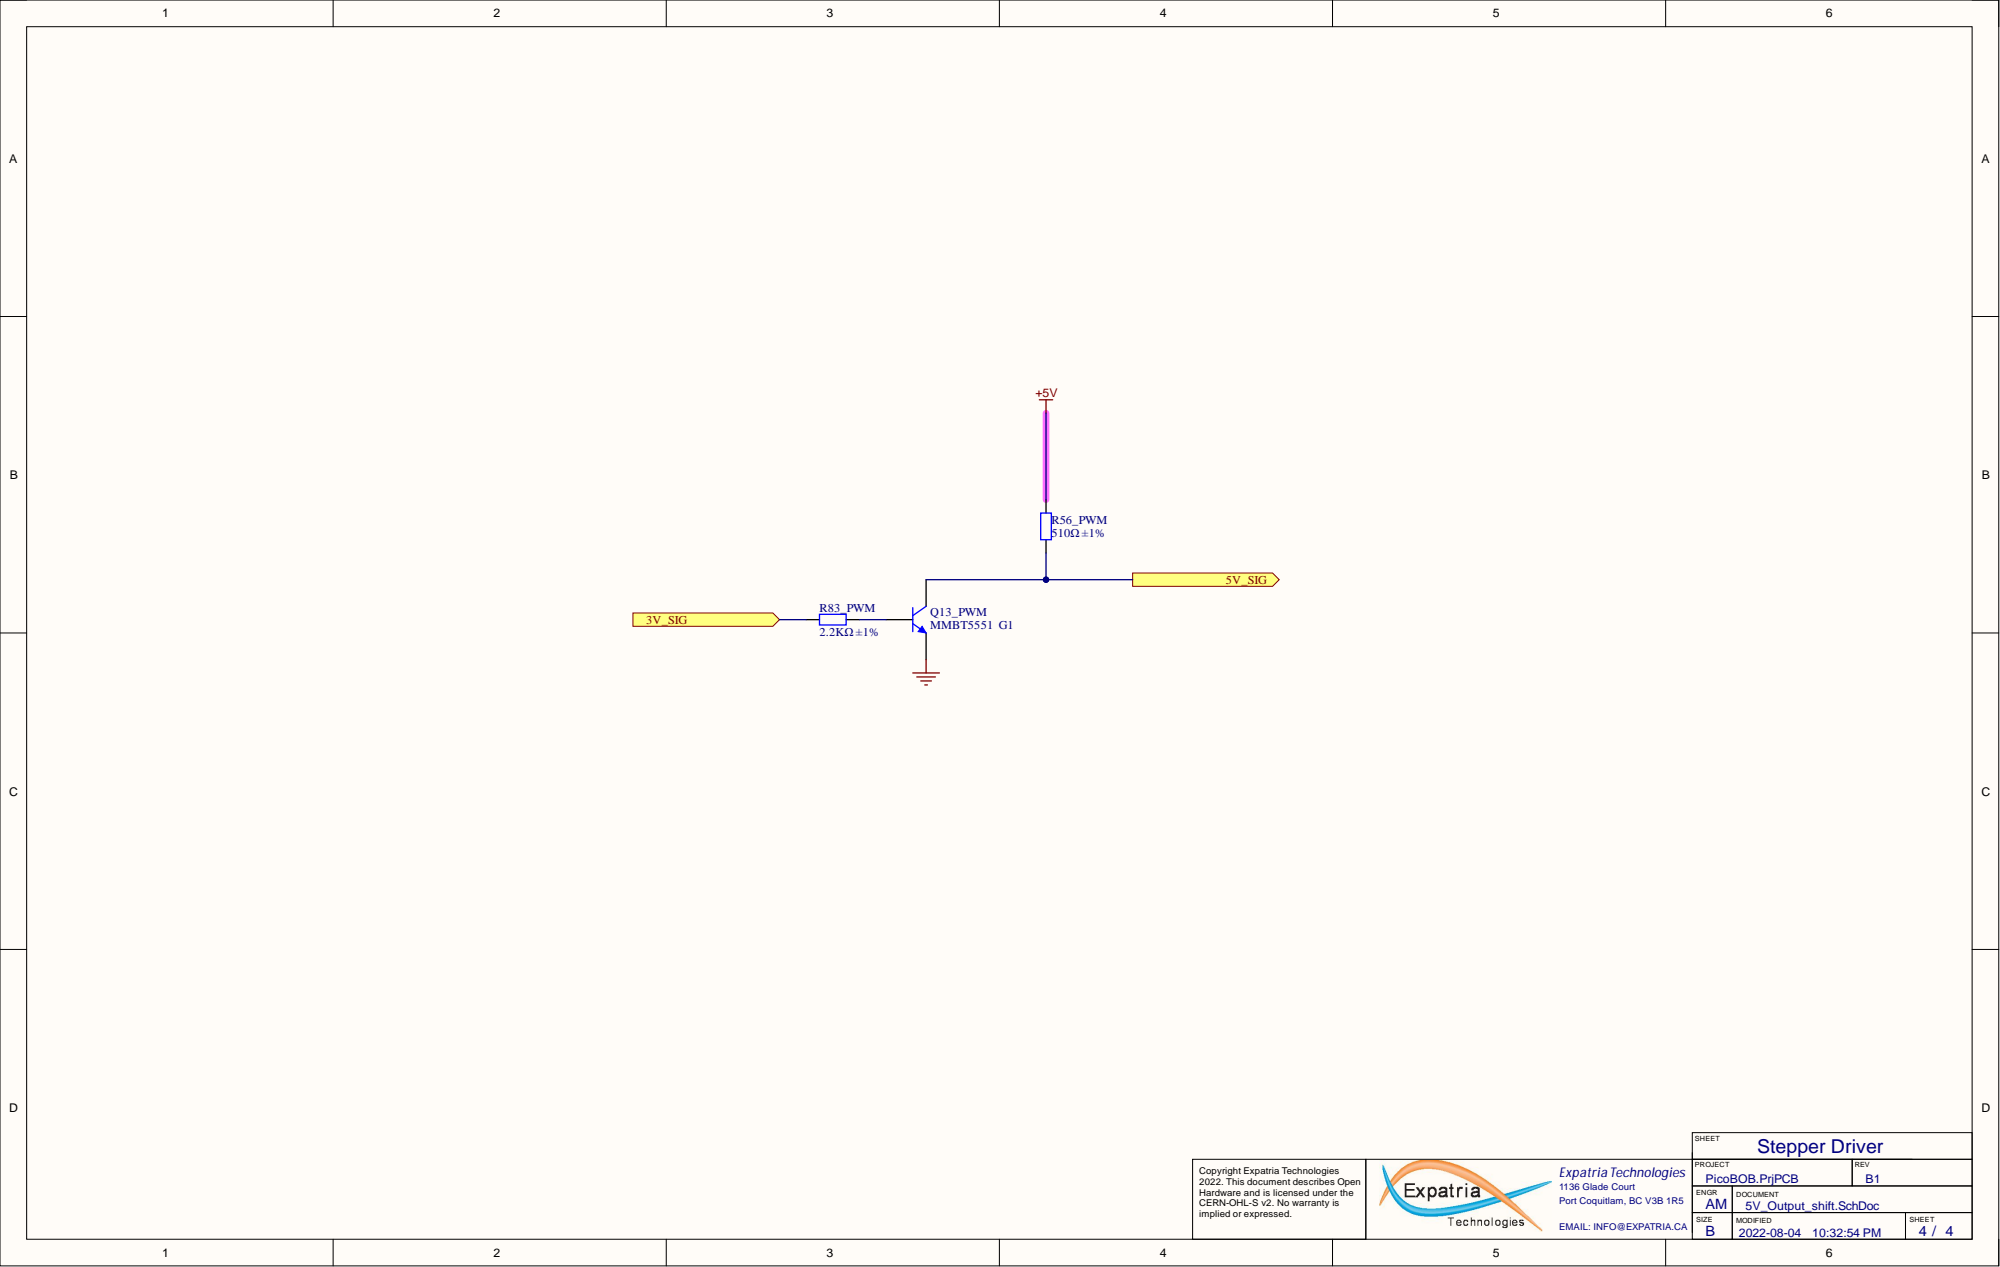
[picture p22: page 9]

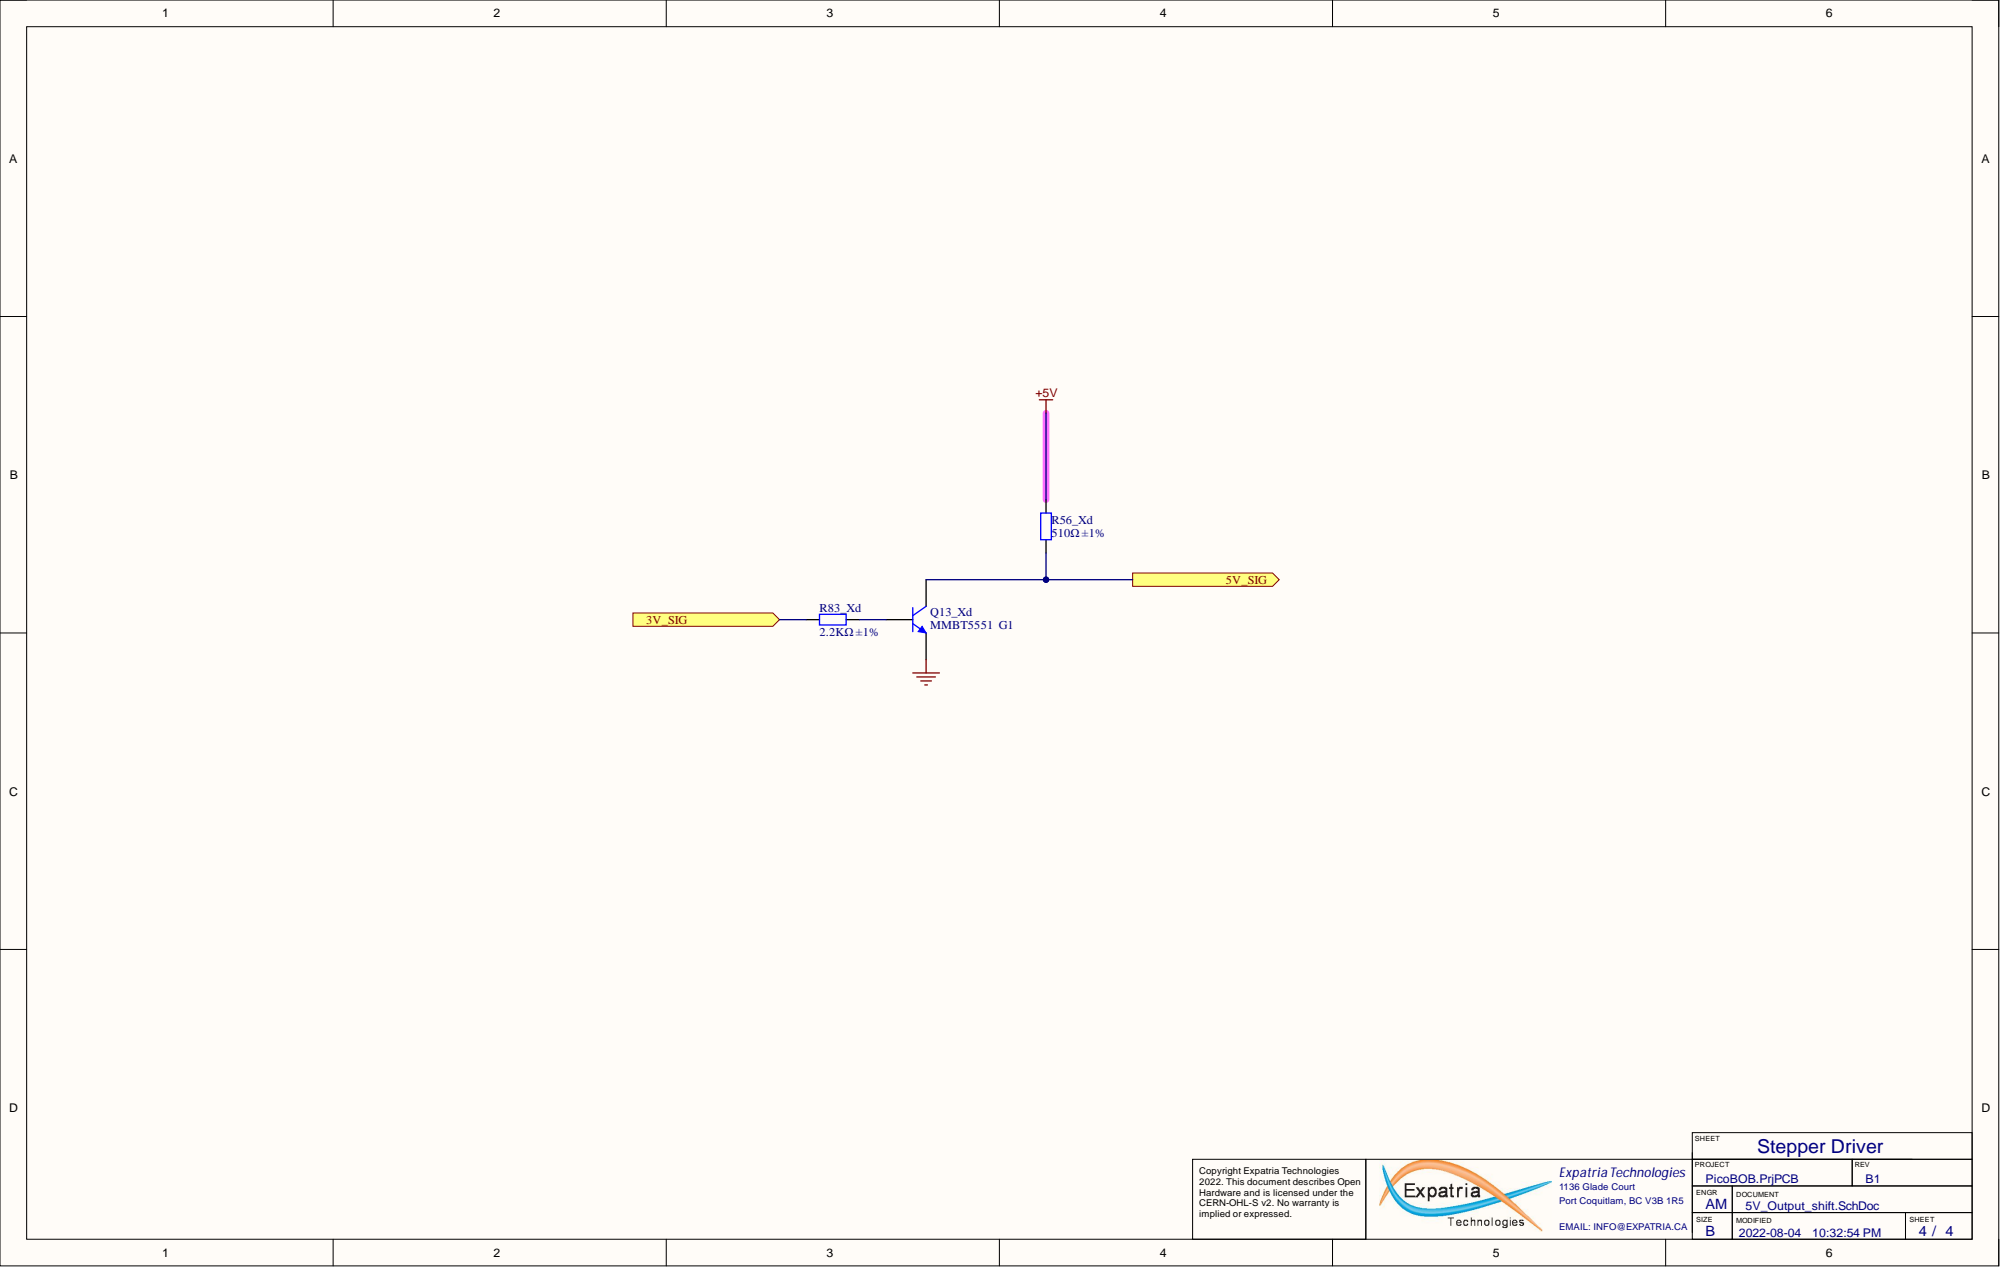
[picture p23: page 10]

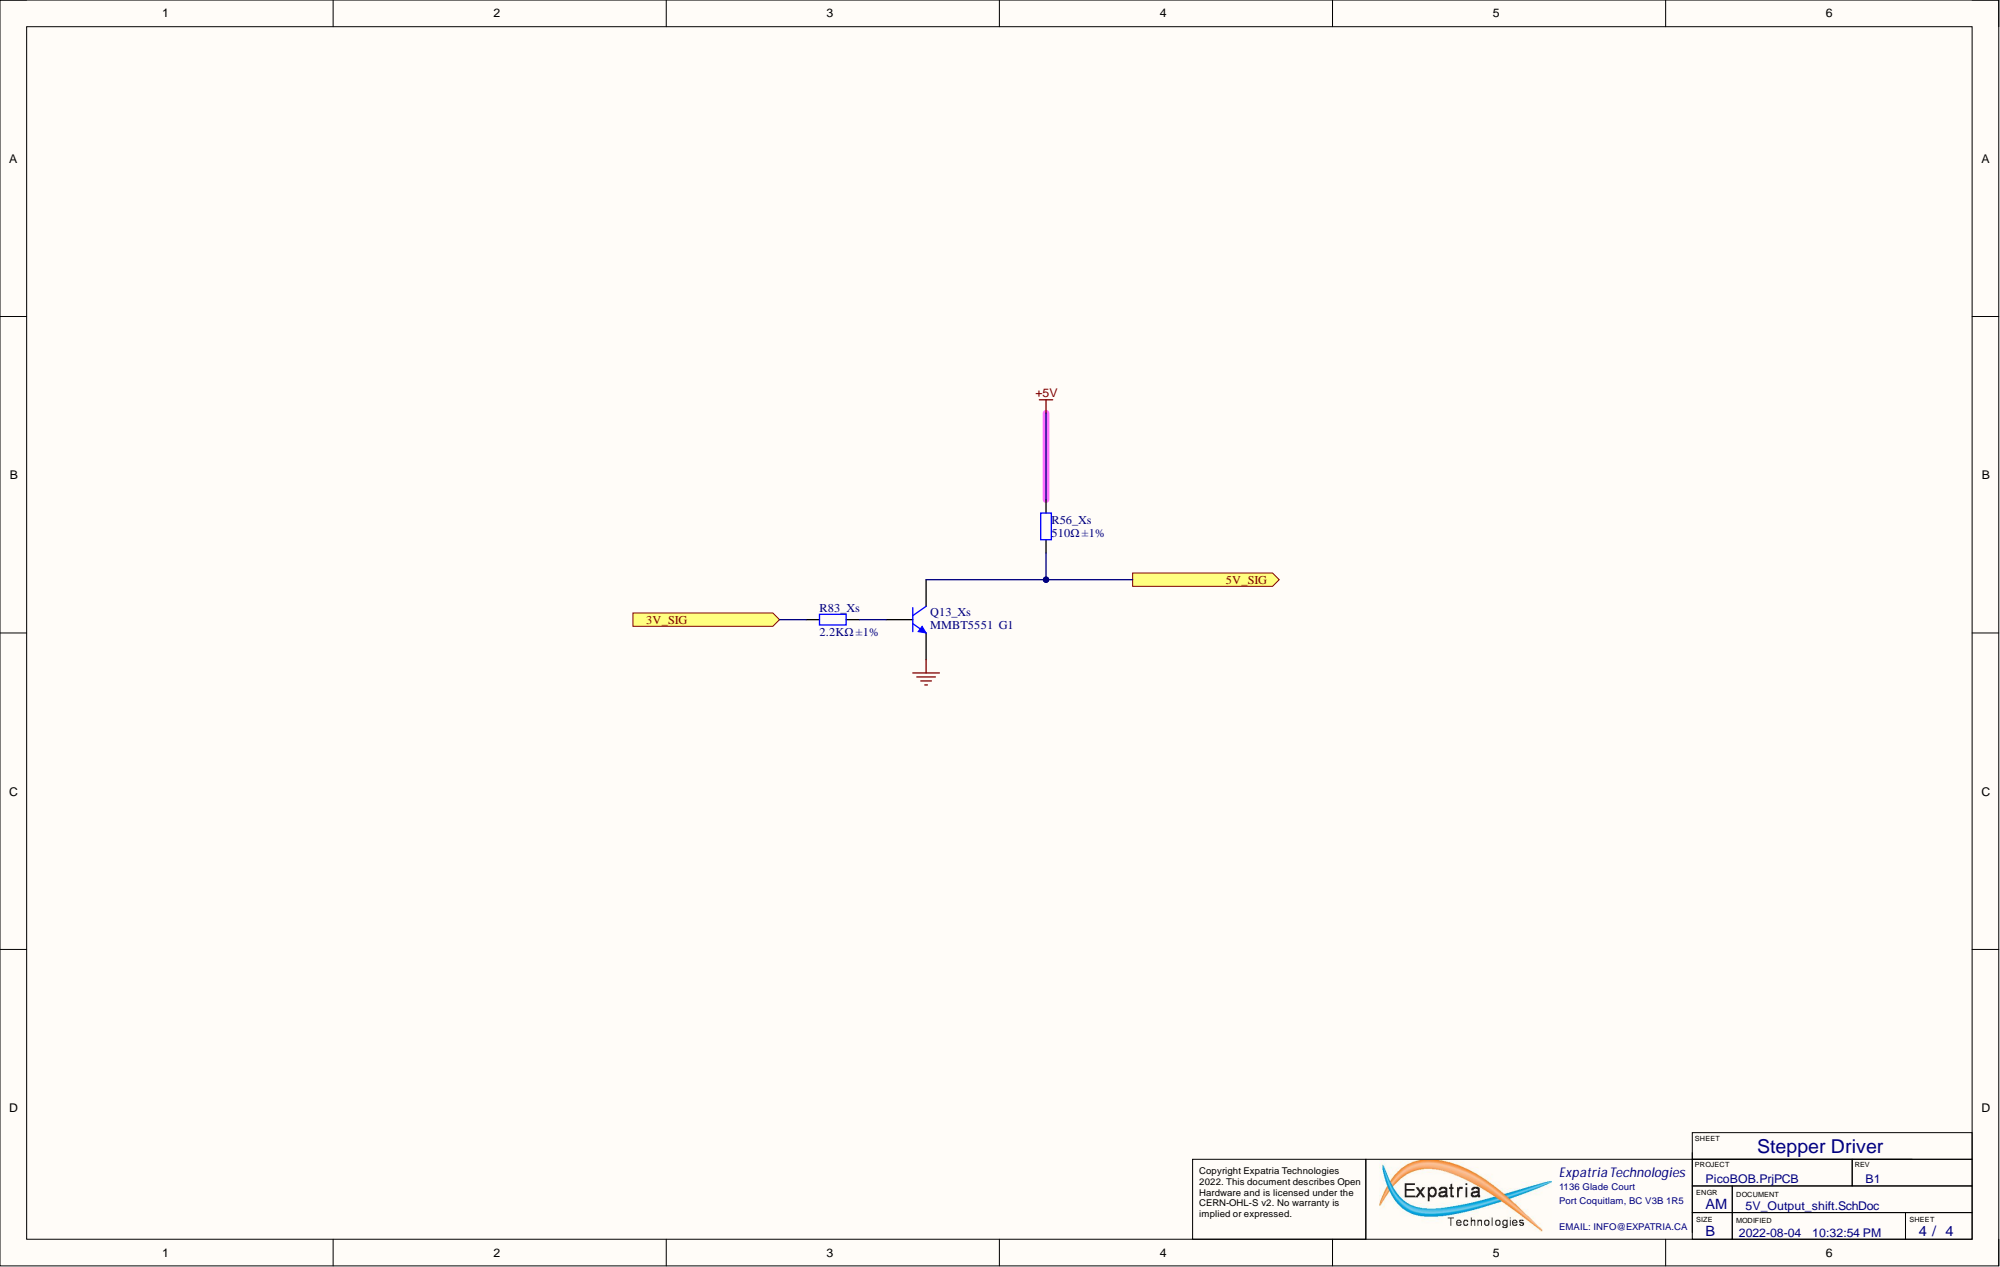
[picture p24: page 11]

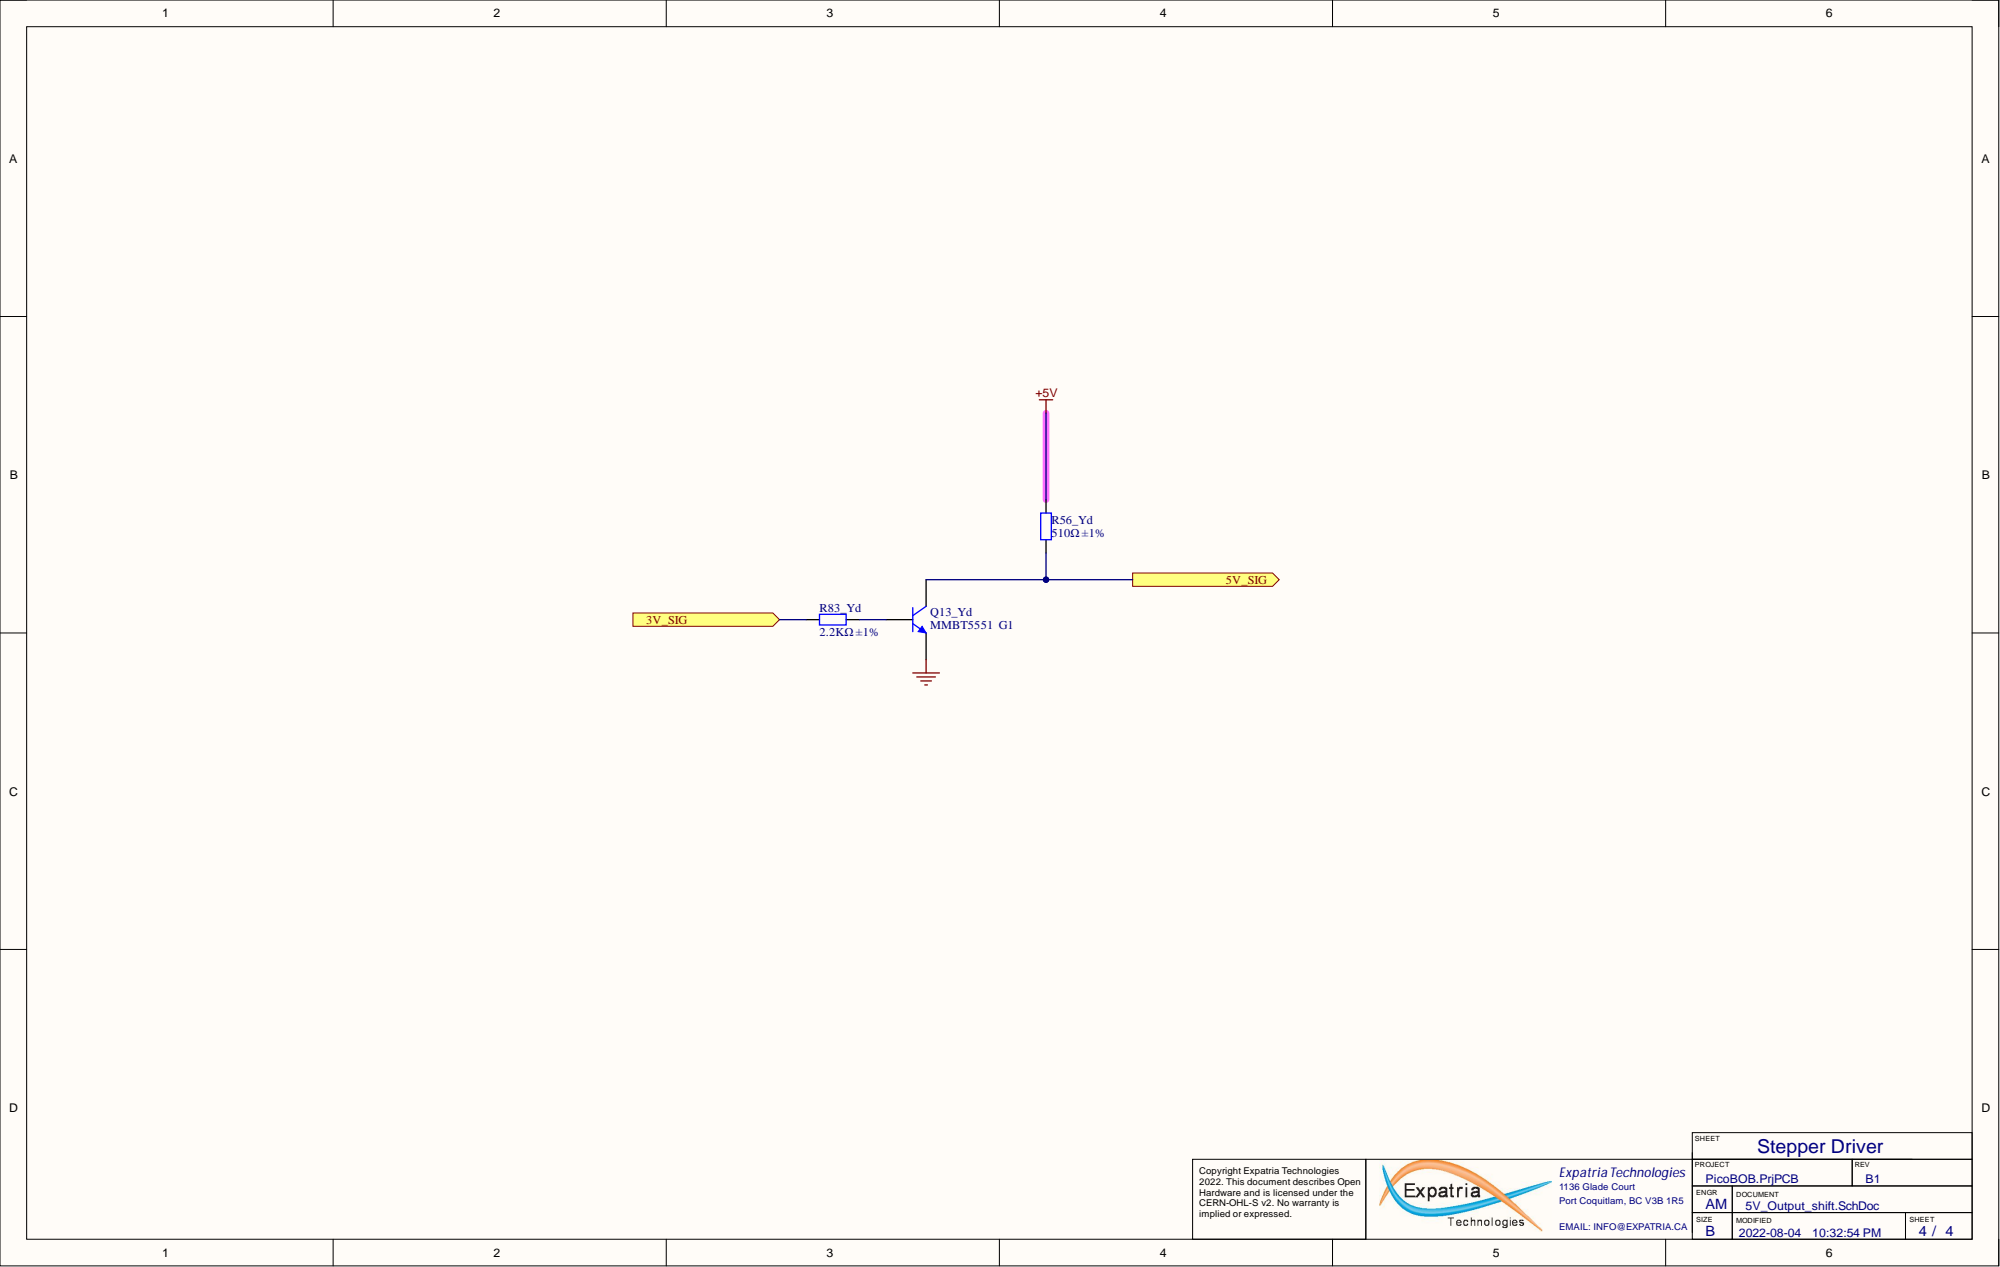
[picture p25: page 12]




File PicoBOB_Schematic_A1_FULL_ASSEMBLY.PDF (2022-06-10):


warra nty i s m p l e d or x pre . | | P OJE PicoBOB.Prj | R V A1

B Copyright Expatria Technologies 2021. This document describes Open Hardware and is licensed under the CERN-OHL-P v2. No

Expatria Technologies 1136 Glade Court

N G A | U RasBOB_board.Sc h D o c


Co yri g ht Ex atri Te n 1. Th nt cri b n Hardware a d i s l er th e CERN-OHL-P v 2. No

5V_Output_shif t












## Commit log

2021-10-24 Initial commit of design files.
    [5V_Output_shift.SchDoc, Change Log.SchDoc, PicoBOB.PrjPCB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]
2021-10-24 Commit schematic PDF.
2022-01-28 Commit pinout image
    [PicoBOB.PrjPCB]
2022-06-10 Updated schematic page numbers.
    [5V_Output_shift.SchDoc, Change Log.SchDoc, RasBOB_board.SchDoc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]
2022-07-13 Fix shared pin between relay and B axis direction
2022-07-13 Commit ascii versions of design files.
    [5V_Output_shift.SchDoc, PicoBOB.PrjPCB, RasBOB_board.SchDoc]
2022-08-05 Commit B1 revision with bare RP2040.
    [5V_Output_shift.SchDoc, Change Log.SchDoc, PicoBOB.PrjPCB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]
2022-09-09 Commit updated design files.
    [PicoBOB.PrjPCB, PicoBOB_CAM_OUTPUT_B1.csv, PicoBOB_CAM_OUTPUT_B1.xlsx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]
2022-09-10 Commit fixed BOM and CPS for boot/rest switches.
    [PicoBOB_CAM_OUTPUT_B1.csv, PicoBOB_CAM_OUTPUT_B1.xlsx, RP2040_MCU.SchDoc]
2022-09-10 Really fixed BOM issue this time.
    [PicoBOB_CAM_OUTPUT_B1.xlsx]
2022-09-11 Commit B1 schematic PDF.
2023-09-27 Commit step file for B1 board.
2025-03-04 add cdn.
    [PicoBOB.PrjPCB, RasBOB_board.SchDoc]
